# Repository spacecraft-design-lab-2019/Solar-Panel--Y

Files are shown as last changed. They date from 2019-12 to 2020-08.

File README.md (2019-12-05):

# Solar-Panel--Y
KiCad files for -Y board

Requirements:
* 58x64 mm
* See -Ycutout.dxf for board outline, including holes for camera, screws, and killswitches
* 3 mm "rails" run along long side (64 mm) of board - don't place any components here
* On bottom face of board (i.e. the internal side), there are 7mm square posts centered around each corner screw hole, and boards mounted to the outside of these. No components can go within these squares, and no components can be bisected by the boards (so components must be either inside of outside of the boards.) These zones are drawn onto the board design for reference
* In addition to components common to all external boards (solar cells, diodes, MPPT circuit, magnetorquers, flat-flex cable, IC), the -Y board also has 2 killswitches and a patch antenna.
* The killswitches must be mounted so that they are fully depressed at the inner edge of the 3 mm rails
* The patch antenna needs to be somewhere on the external face (same face as the solar cells)
* The flat-flex cable connector needs to remain where it is in the current design (rev2)

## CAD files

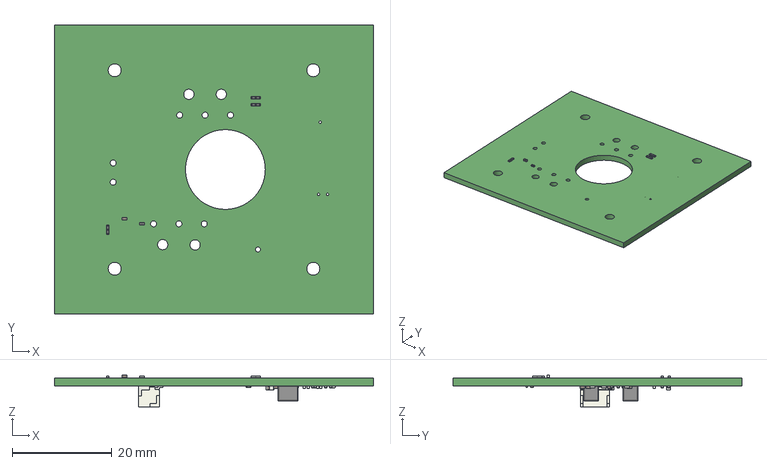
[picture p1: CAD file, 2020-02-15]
ypanel.step
64.0 x 58.0 x 6.40 mm

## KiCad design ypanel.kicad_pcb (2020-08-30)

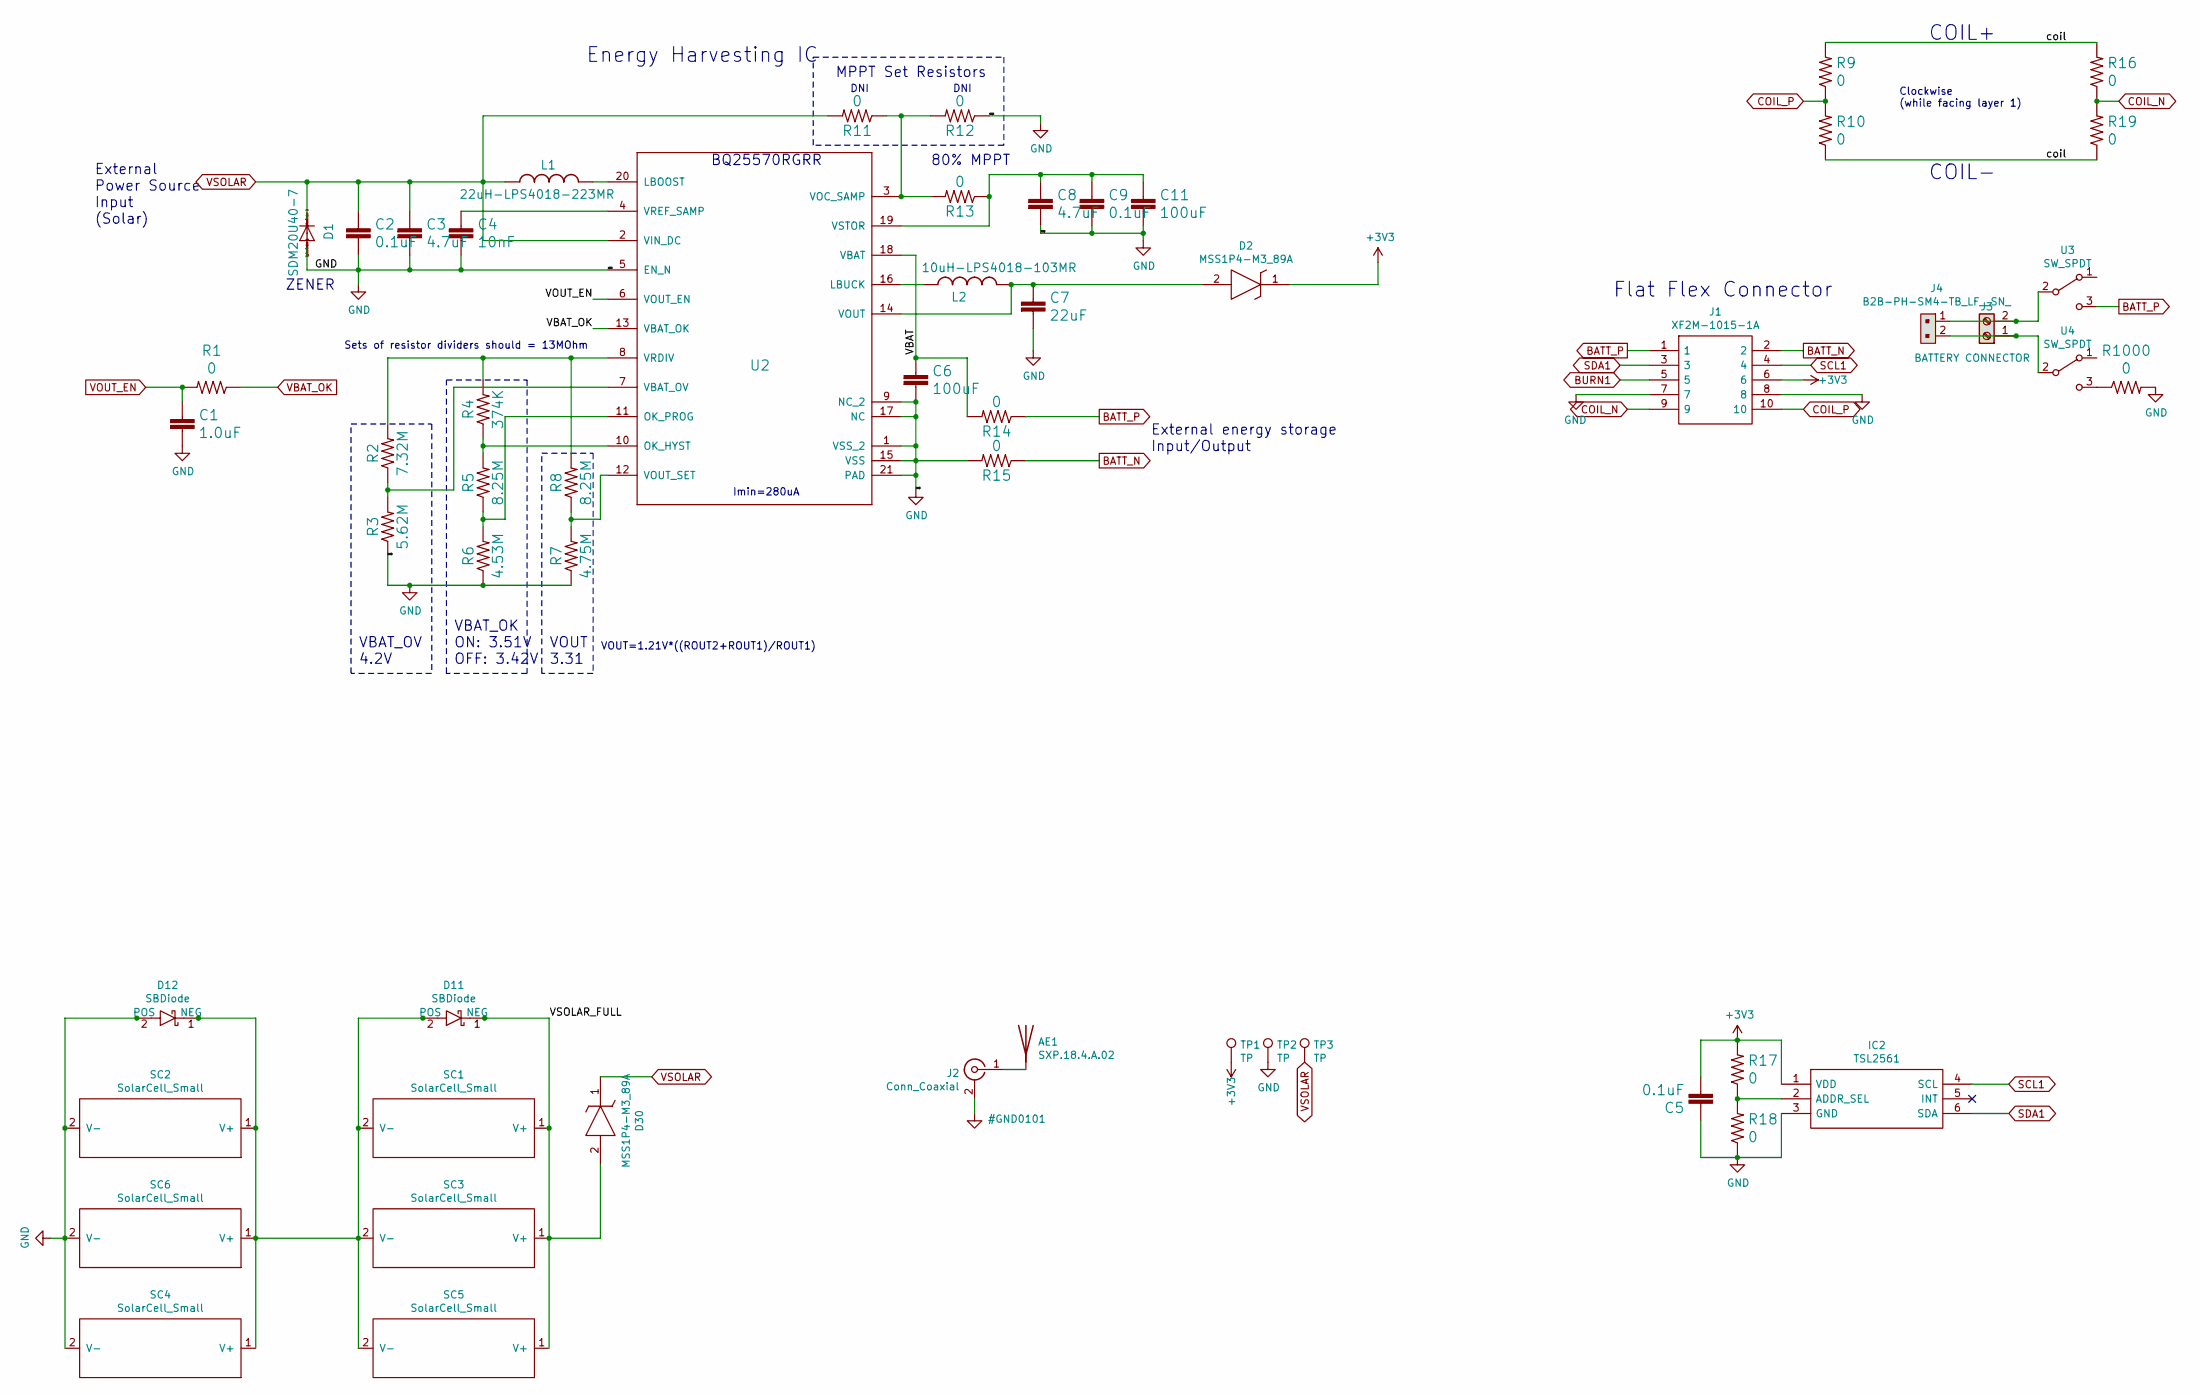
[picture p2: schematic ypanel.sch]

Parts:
AE1: SXP.18.4.A.02
C1: 1.0uF; C_0402_1005Metric
C2, C5, C9: 0.1uF; C_0402_1005Metric
C3, C8: 4.7uF; C_0402_1005Metric
C4: 10nF; C_0402_1005Metric
C6, C11: 100uF; C_0603_1608Metric
C7: 22uF; C_0402_1005Metric
D1: SDM20U40-7; SOD523
D2, D30: MSS1P4-M3_89A; MICROSMP; Manufacturer_Part_Number MSS1P4-M3/89A; Mouser Part Number 625-MSS1P4-M3
D11, D12: SBDiode; SB Diode
IC2: TSL2561; Manufacturer_Part_Number TSL2561; Mouser Part Number N/A
J1: XF2M-1015-1A; Manufacturer_Part_Number XF2M-1015-1A; Mouser Part Number 653-XF2M-1015-1A
J2: Conn_Coaxial; U.FL_Hirose_U.FL-R-SMT-1_Vertical
J3: BATTERY CONNECTOR; SCREWTERMINAL-3.5MM-2_LOCK
J4: B2B-PH-SM4-TB_LF__SN_; JST_PH_B2B-PH-SM4-TB_1x02-1MP_P2.00mm_Vertical; MPN B2B-PH-SM4-TB(LF)(SN); Digi-Key_PN 455-1734-1-ND
L1: 22uH-LPS4018-223MR; LPS4018
L2: 10uH-LPS4018-103MR; LPS4018
R1, R9, R10, R11, R12, R13, R14, R15, R16, R17, R18, R19, R1000: 0; R_0402_1005Metric
R2: 7.32M; R_0402_1005Metric
R3: 5.62M; R_0402_1005Metric
R4: 374K; R_0402_1005Metric
R5, R8: 8.25M; R_0402_1005Metric
R6: 4.53M; R_0402_1005Metric
R7: 4.75M; R_0402_1005Metric
SC1, SC2, SC3, SC4, SC5, SC6: SolarCell_Small; KXOB25-05X3F
TP1, TP2, TP3: TP; TestPoint_THTPad_D1.0mm_Drill0.5mm
U2: Value; QFN50P350X350X100-21N-D
U3: SW_SPDT; D2F-L2-2
U4: SW_SPDT; D2F-L2

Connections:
+3V3: C5.2, D2.1, IC2.1 (VDD), J1.6, R17.2, TP1.1
/VBAT: C6.1, R14.2, U2.18 (VBAT)
/VSOLAR_FULL: D11.1 (NEG), D30.2, SC1.1 (V+), SC3.1 (V+), SC5.1 (V+)
/coil: R9.2, R10.1, R16.2, R19.1
BATT_N: J1.2, R15.1
BATT_P: J1.1, R14.1, U3.3 (C)
BURN1: J1.5
COIL_N: J1.9, R16.1, R19.2
COIL_P: J1.10, R9.1, R10.2
unnamed: AE1.1, J2.1 (In)
unnamed: C4.1, U2.4 (VREF_SAMP)
unnamed: C7.1, D2.2, L2.2, U2.14 (VOUT)
unnamed: C8.1, C9.1, C11.1, R13.1, U2.19 (VSTOR)
unnamed: D11.2 (POS), D12.1 (NEG), SC1.2 (V-), SC2.1 (V+), SC3.2 (V-), SC4.1 (V+), SC5.2 (V-), SC6.1 (V+)
unnamed: IC2.2 (ADDR_SEL), R17.1, R18.2
unnamed: J3.1, J4.2, U4.2 (B)
unnamed: J3.2, J4.1, U3.2 (B)
unnamed: L1.2, U2.20 (LBOOST)
unnamed: L2.1, U2.16 (LBUCK)
unnamed: R2.1, R3.2, U2.7 (VBAT_OV)
unnamed: R2.2, R4.2, R8.2, U2.8 (VRDIV)
unnamed: R4.1, R5.2, U2.10 (OK_HYST)
unnamed: R5.1, R6.2, U2.11 (OK_PROG)
unnamed: R7.2, R8.1, U2.12 (VOUT_SET)
unnamed: R11.1, R12.2, R13.2, U2.3 (VOC_SAMP)
unnamed: R1000.1, U4.3 (C)
SCL1: IC2.4 (SCL), J1.4
SDA1: IC2.6 (SDA), J1.3
VBAT_OK: R1.1, U2.13 (VBAT_OK)
VOUT_EN: C1.1, R1.2, U2.6 (VOUT_EN)
VSOLAR: C2.1, C3.1, D1.C, D30.1, L1.1, R11.2, TP3.1, U2.2 (VIN_DC)

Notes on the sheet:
Flat Flex Connector
DNI
ZENER
VOUT 3.31
80% MPPT
VBAT_OK ON: 3.51V OFF: 3.42V
Imin=280uA
External Power Source Input (Solar)
External energy storage Input/Output
BQ25570RGRR
Energy Harvesting IC
VBAT_OV 4.2V
Sets of resistor dividers should = 13MOhm
VOUT=1.21V*((ROUT2+ROUT1)/ROUT1)
MPPT Set Resistors
COIL+
COIL-
Clockwise (while facing layer 1)

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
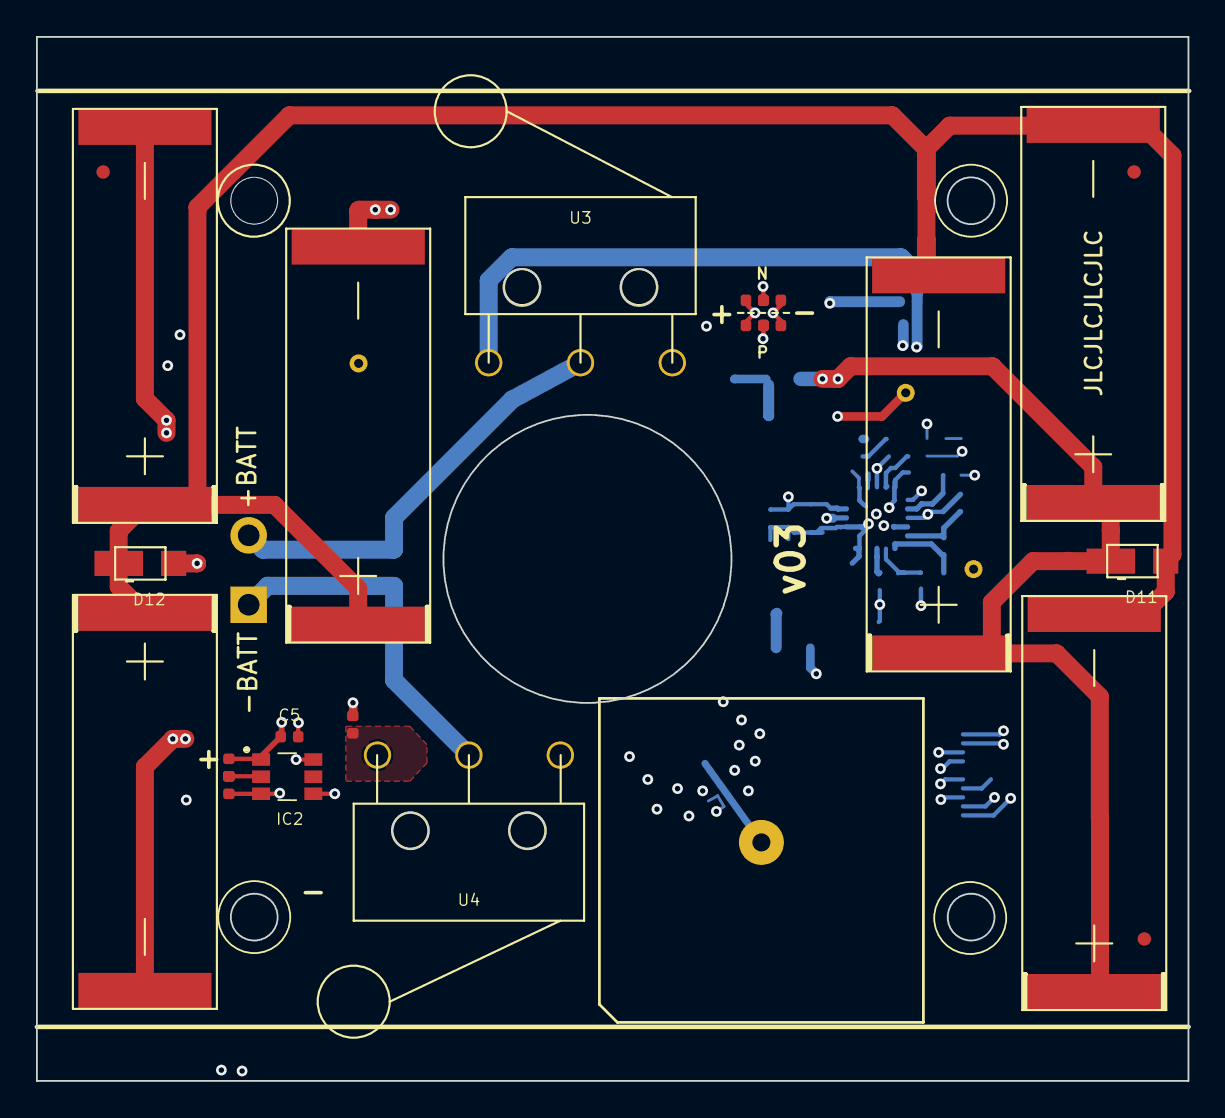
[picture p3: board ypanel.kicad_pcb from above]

Board: 6 copper layers, 64.0 x 58.0 mm, 55 parts (0 on the bottom side), 31 nets.

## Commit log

2019-10-21 Added -Y PCB files (still in progress)
2019-10-23 Updated -Y PCB design
2019-10-24 Incorporated patch antenna and switches
2019-10-25 Added finished version 1 of -Y PCB
2019-10-25 starting on -Y board
    [solarpcb.sch, solarpcd.kicad_pcb, solarpcd.sch]
2019-10-25 killer coils
    [solarpcd.kicad_pcb, solarpcd.sch]
2019-10-26 -Y board finished
    [solarpcd.kicad_pcb, solarpcd.sch]
2019-10-26 zipped fabrication files for all but +Y
    [solarpcd-B_Mask.gbs, solarpcd-B_Paste.gbp, solarpcd-B_SilkS.gbo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]
2019-10-26 JLCPCB fab output
    [solarpcd-B_Mask.gbr, solarpcd-B_Paste.gbr, solarpcd-B_SilkS.gbr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]
2019-10-29 Added step file of -Y panel
    [solarpanel-Y.step]
2019-10-30 Updated step file with additional 3D part models
    [PCB-y.stp]
2019-10-31 Added killswitches to step file
    [PCB-y.stp]
2019-11-14 Changed board outline to account for structures requirements
    [solarpcd.kicad_pcb]
2019-12-03 Updated -Y PCB Layout
    [solarpcd.kicad_pcb]
2019-12-03 Modified -Y Layout
    [solarpcd.kicad_pcb]
2019-12-20 v01 order + repo overhaul
    [solarpcb.sch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]
2020-02-12 repaired schematic so it matches PCB
    [ypanel.kicad_pcb, ypanel.sch]
2020-02-12 Updated -Y
    moved killswitches & flat-flex connector to new locations
    [ypanel.kicad_pcb, ypanel.sch]
2020-02-13 Added step file of -Y
    [ypanel.step]
2020-02-15 Added new antenna to -Y
    [PCB-y.stp, ypanel.kicad_pcb, ypanel.sch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]
2020-02-20 updated 3d footprint paths and generated new step file
    [ypanel.kicad_pcb]
2020-02-23 fixed antenna footprint and regenerated step file
    [ypanel.kicad_pcb, ypanel.sch]
2020-02-26 moved camera hole and other components
    [ypanel.kicad_pcb]
2020-02-28 Changed magnetorquer coils
    [ypanel.kicad_pcb]
2020-02-29 design review and gerber generation
    [ypanel-B.Mask.gbr, ypanel-B.SilkS.gbr, ypanel-Bottom.gbr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]
2020-03-01 added fiducials, regenerated 3d model and gerbers
    [-Ycutout.dxf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]
2020-08-29 clean up & manufacturing output for v2
    [ypanel-B.Mask.gbr, ypanel-B.SilkS.gbr, ypanel-B_Mask.gbr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]
2020-08-29 clean up & manufacturing output for v3
    [ypanel-B.Mask.gbr, ypanel-B.SilkS.gbr, ypanel-B_Mask.gbr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]
2020-08-29 should actually be v3
    [ypanel-B_Mask.gbr, ypanel-B_Paste.gbr, ypanel-B_SilkS.gbr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]
2020-08-30 fixing coil-to-board-edge distance...
    [ypanel.kicad_pcb]
2020-08-30 -y panel coils fixed and manufacturing files generated
    [ypanel-B_Mask.gbr, ypanel-B_Paste.gbr, ypanel-B_SilkS.gbr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]
2020-08-30 v3 out for order
    [ypanel.kicad_pcb]
